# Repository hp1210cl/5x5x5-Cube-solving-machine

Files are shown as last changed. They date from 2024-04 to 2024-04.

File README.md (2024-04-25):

# 5x5x5 Cube solving machine

# 五阶解魔方机

一种自动复原5阶魔方的机器设计。A design of auto solving 5x5x5 cube machine.

*目前是已公开的最快的5阶解魔方机。The fastest 5x5x5 cube solving machine now.*

演示视频(demo video)：[三轴五阶解魔方机运行展示_哔哩哔哩_bilibili](https://www.bilibili.com/video/BV1yZ421n7nz/)

细节视频(detail video)：[3轴五阶解魔方机细节展示_哔哩哔哩_bilibili](https://www.bilibili.com/video/BV1LF4m1A7hH/)

### 1.整体架构

整个设计分为硬件和软件。

##### 1.1硬件部分

由框架、旋转器、推进器、arduino控制板和驱动板组成。

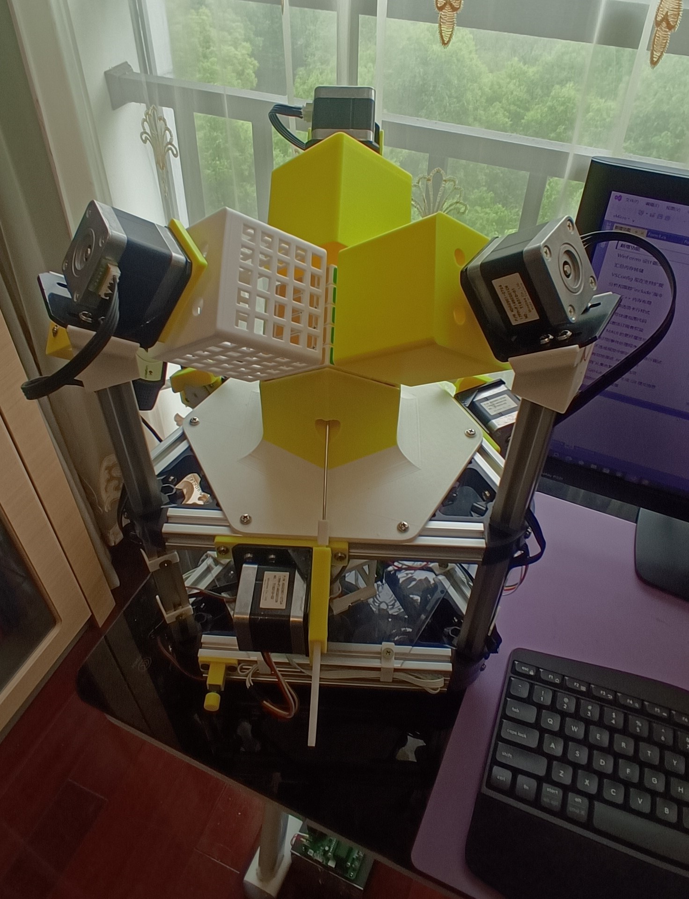
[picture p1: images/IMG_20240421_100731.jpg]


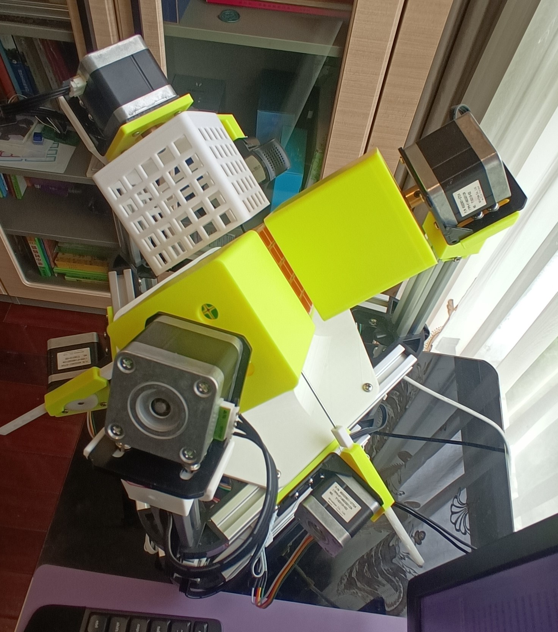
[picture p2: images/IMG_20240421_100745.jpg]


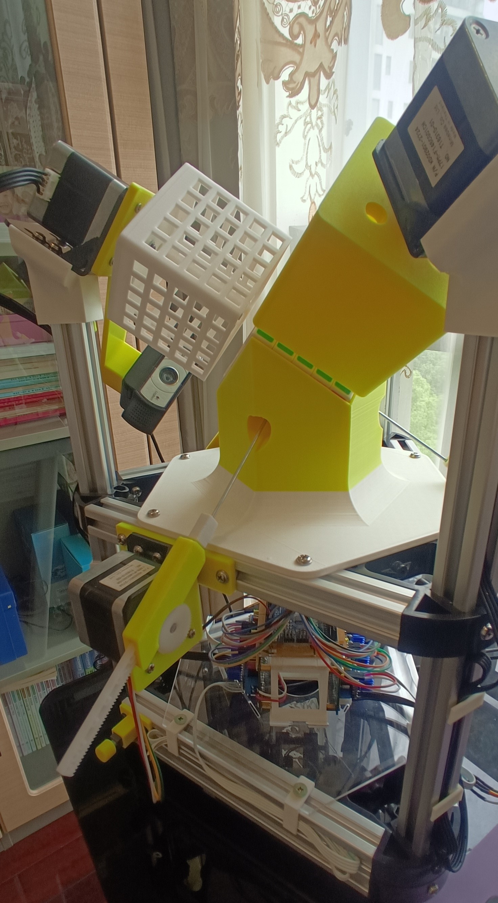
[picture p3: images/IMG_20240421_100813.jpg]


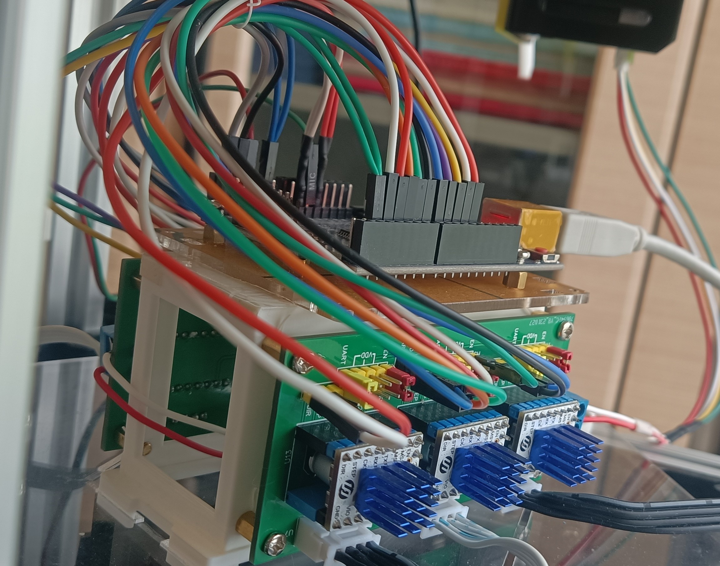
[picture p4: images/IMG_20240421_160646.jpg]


#### 1.2软件部分

由arduino下位机和PC上位机组成。

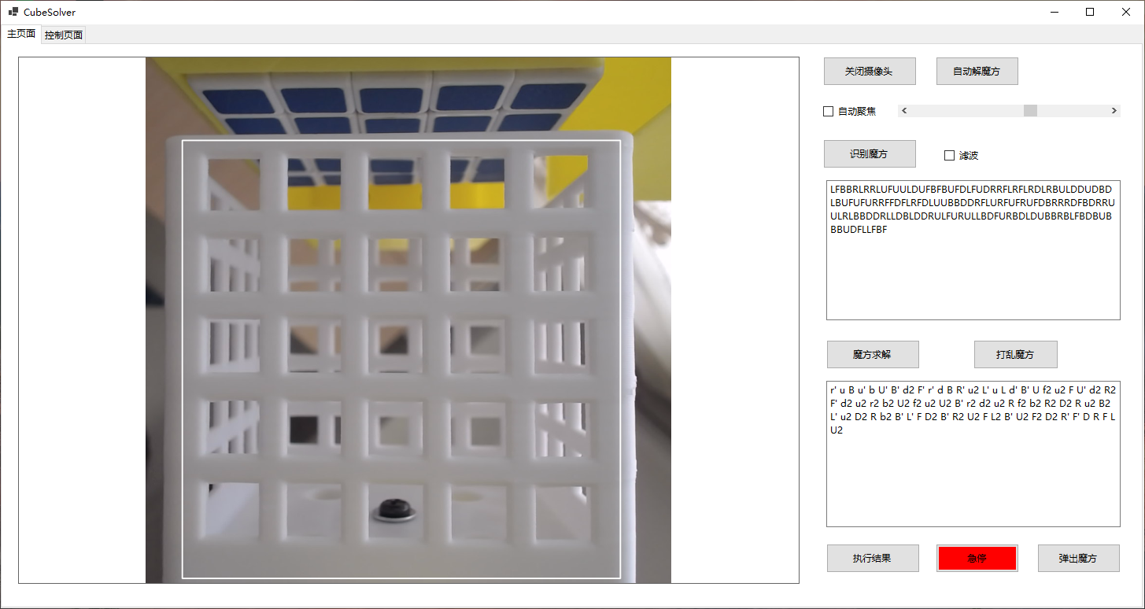
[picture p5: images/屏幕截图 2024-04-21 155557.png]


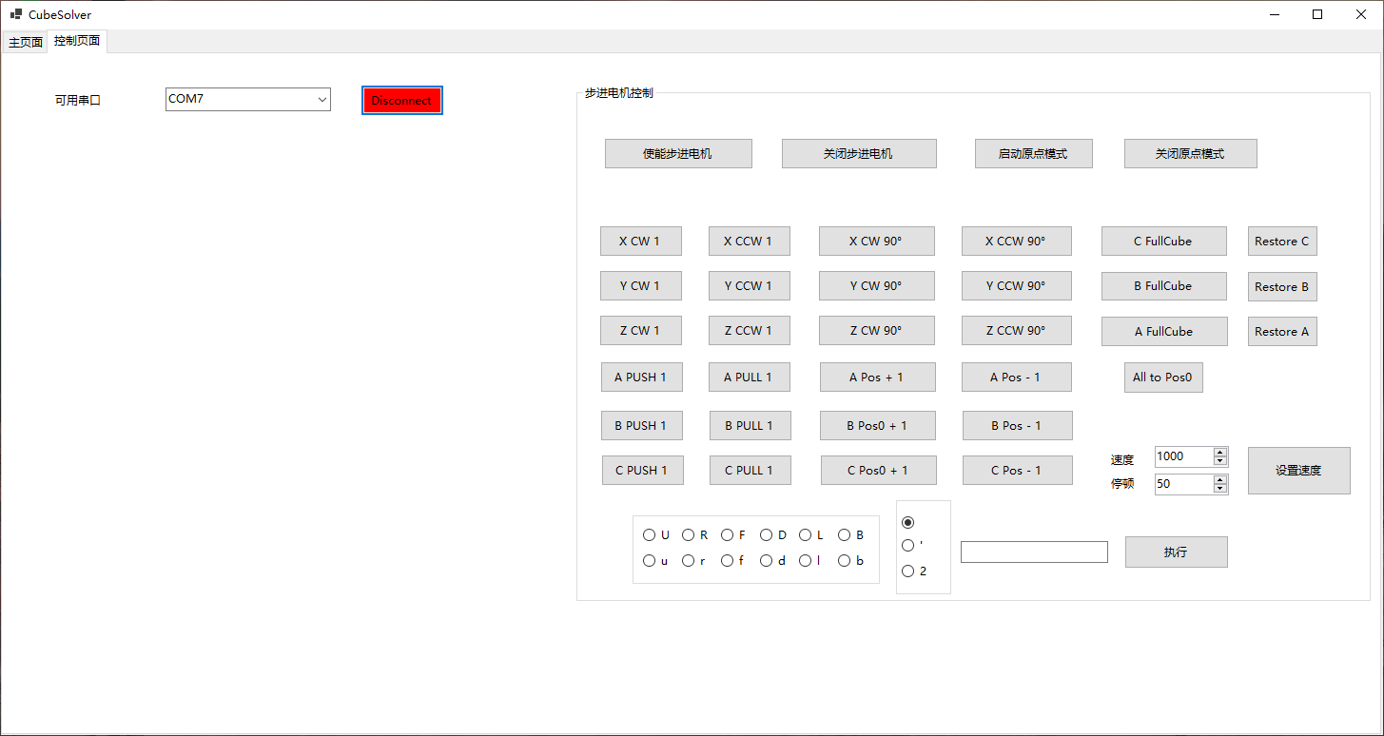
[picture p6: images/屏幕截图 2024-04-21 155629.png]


arduino下位机负责控制步进电机运动，PC上位机负责颜色识别、魔方求解、下位机控制等。

PC上位机使用VS2022 C#编写。

魔方求解使用了**陈霜**的五阶魔方算法，此算法是目前世界上最快的5阶算法，在此向他致敬！详情可以去他的github了解：[cs0x7f/cube555: 5x5x5 solver (github.com)](https://github.com/cs0x7f/cube555)，我也改写了c#版本：[hp1210cl/cube555-solver: C# version of Chen Shuang's Five-phase-reduction 5x5x5 solver (github.com)](https://github.com/hp1210cl/cube555-solver)。

颜色识别使用了EmguCV。

### 2.解魔方情况

对于一个打乱的5阶魔方，算法给出的步骤一般在70步左右。机器从识别-求解-复原全过程需耗时在90秒之内，典型时间75秒。

### 3.如何运行

#### 3.1硬件搭建

安装BOM清单准备好材料，按照图片成品组装。

#### 3.2下位机准备

将controller文件夹中的arduino程序刷入开发板。

#### 3.3运行上位机

将摄像头、arduino连接到PC，使用Visual Studio打开cubesolver文件夹下的工程文件，编译，运行。先打开摄像头，再在上位机控制选项卡页面连接开发板，再使能步进电机，进行机器的调试。

#### 3.4开始解魔方

如果出现卡滞，可以使用硬件紧急停止按钮，也可以使用上位机软件的急停按钮（有延时）。

### 4.调试细节

解魔方机需要精确调试才能顺利运行，具体调试详见调试文档。

###

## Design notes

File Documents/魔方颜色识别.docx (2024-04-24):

一、一些约定

1.X旋转器对着U，负责UD面的旋转，Y旋转器对着L，负责LR面的旋转，Z旋转器对着F，负责FB面的旋转。

2.A推杆负责UD层的控制，B推杆负责LR层的控制，C推杆负责FB层的控制。

3.魔方描述字符串采用标准的URFDLB定义。

4.以下顺时针逆时针是指面向旋转器看向步进电机，旋转器的转动方向。

二、识别控制流程

1.C推杆推送魔方到最高位，摄像头拍照得到Image1，Z旋转器顺时针整体转动魔方90度，摄像头拍照得到Image2，Z旋转器再次顺时针整体转动魔方90度，摄像头拍照得到Image3，Z旋转器再次顺时针整体转动魔方90度，摄像头拍照得到Image4，C推杆回位。

2.B推杆推送魔方到最高位，Y旋转器顺时针整体转动魔方90度，B推杆回位。

3.C推杆推送魔方到最高位，摄像头拍照得到Image5，Z旋转器顺时针整体转动魔方180度，摄像头拍照得到Image6.

三、识别方法

1.以上得到的6张照片，经过旋转（逆时针45度）、裁剪得到6张魔方单面的图片，就是魔方URFDLB表示法的视图。

2.当前魔方的U面是Image5（没有旋转变化），L面是Image1（旋转180度），F面是Image2（旋转180度），D面是Image6（旋转180度），R面是Image3（旋转180度），B面是Image4（旋转180度）。

3.每张图片有25个色块，判断每个色块的颜色，从左至右，从上至下，排列就得到面的描述字符串。

注：只针对摄像头特定安装位置（步进电机引出支架安装法）

四、颜色识别

1.将魔方单面的图片转换为HSV色域。

2.先按照黄色使用InRange将HSV图片二值化。

3.将二值化图片开操作去除白点。

4.将开操作的图片再闭操作去除黑点。

5.在闭操作的图片中查找轮廓。

6.对于每个色块的中心点，判断它是不是在这些轮廓中，如果在，那么这个色块就是黄色。

7.再按照红色、蓝色、橙色、绿色，重复1-6步。

8.剩下没有识别的色块就是白色。

9.对于U面，需要倒序，才是正确的面的描述字符串。

10.按照URFDLB的顺序，将面的描述字符串连接起来就是魔方的描述字符串。

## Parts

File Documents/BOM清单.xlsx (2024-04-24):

序号 | 名称 | 规格 | 数量 | 备注 | 示例图片
1 | 步进电机 | 42型 | 6 | 选用低内阻大扭矩高速型号，最好出轴长度12mm
2 | 六角联轴器 | 5mm | 3 | 铜 | #VALUE!
3 | 步进电机支架 | 42型 | 6 |  | #VALUE!
4 | 齿条 | 0.5m | 3 | 125*7*4mm | #VALUE!
5 | 齿轮 | 0.5m | 3 | 50齿，POM | #VALUE!
6 | Arduino模块 |  | 1 | UNO R3，其他开发板也可以 | #VALUE!
7 | TMC2209驱动模块 |  | 6 | 富源盛TMC2209 | #VALUE!
8 | 驱动底板 |  | 2 | 嘉立创免费制作 | #VALUE!
9 | 自锁开关 |  | 1 | 8x8.5x8.5 | #VALUE!
10 | 摄像头 | 罗技C930 | 1 | 其他型号也可以，1080P，有安装底座的最好
11 | 铝型材 | 20型 |  | 205mm的6根，350mm的3根
12 | 三角洲3D打印机角件 |  | 6 | 现在网上货比较少了，可以自行3D打印 | #VALUE!
13 | 螺丝、铝型材T型螺母 | 20型 | 若干 | M4*8 | #VALUE!
14 | 步进电机连接线 |  | 3 | 300mm
15 | 步进电机连接线 |  | 3 | 600mm
16 | 玩具车轴 |  | 3 | 2*80mm，铁 | #VALUE!
17 | 杜邦线 |  | 若干
18 | 24V电源模块 |  |  | 功率60W以上

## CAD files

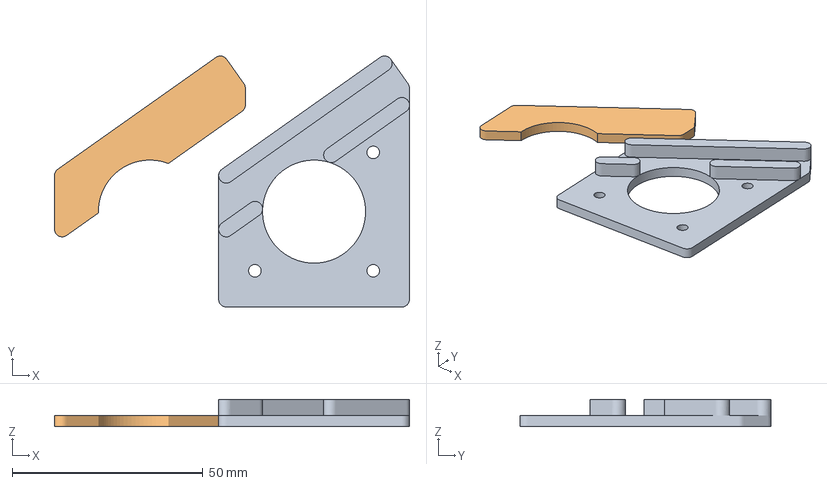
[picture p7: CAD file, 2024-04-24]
3D models/齿条推进支架50齿 v8.3mf
93.0 x 65.8 x 7.20 mm
实体4
实体5

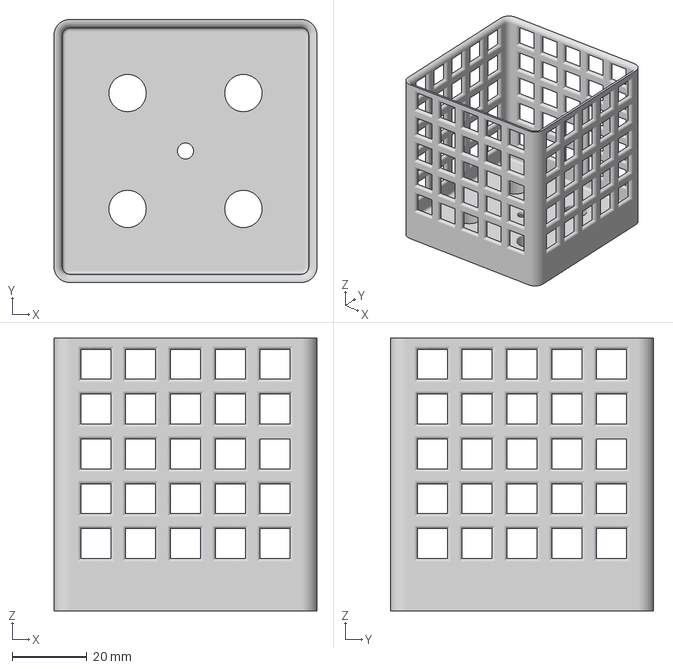
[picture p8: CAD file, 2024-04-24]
3D models/旋转器镂空 v2.3mf
70.4 x 70.4 x 73.0 mm

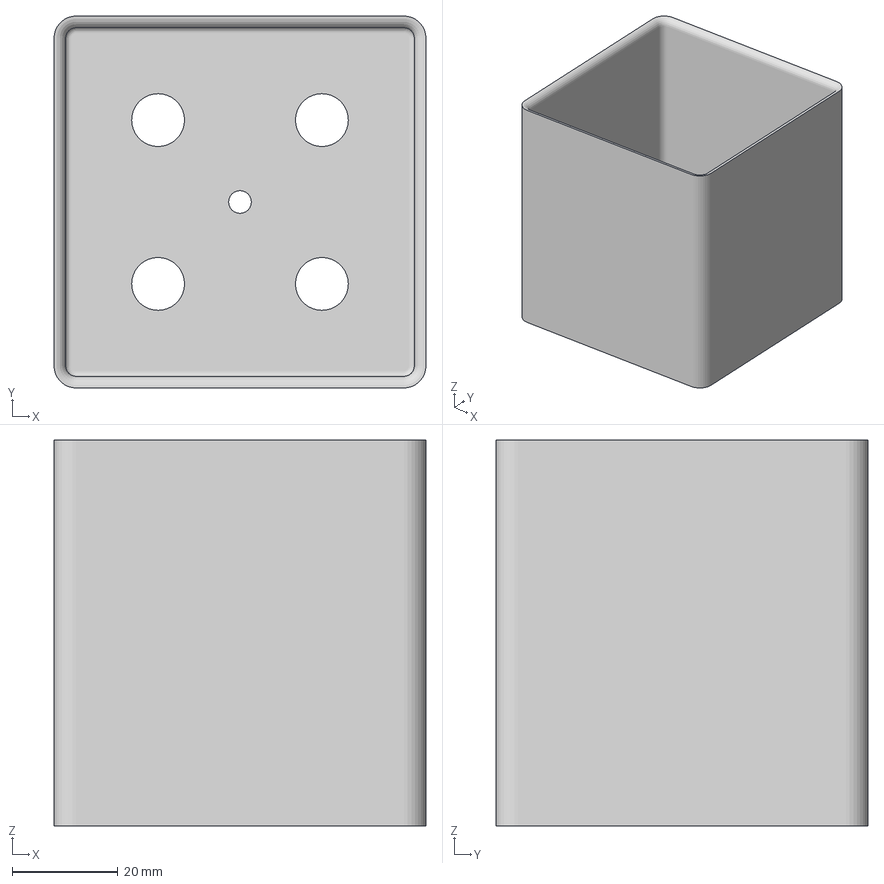
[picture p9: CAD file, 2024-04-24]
3D models/旋转器圆角 v4.3mf
70.4 x 70.4 x 73.0 mm

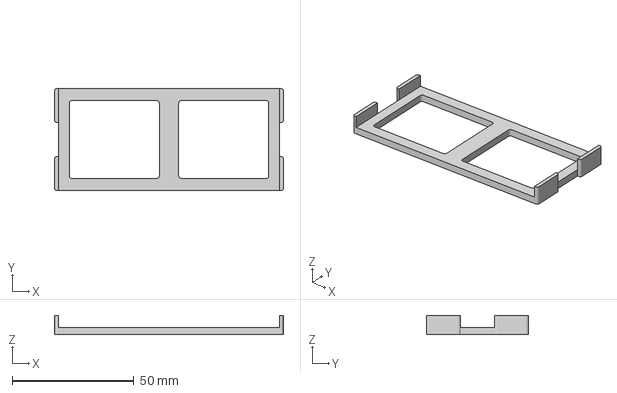
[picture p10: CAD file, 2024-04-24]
3D models/arduino安装架底板 v6.3mf
94.2 x 42.0 x 8.00 mm

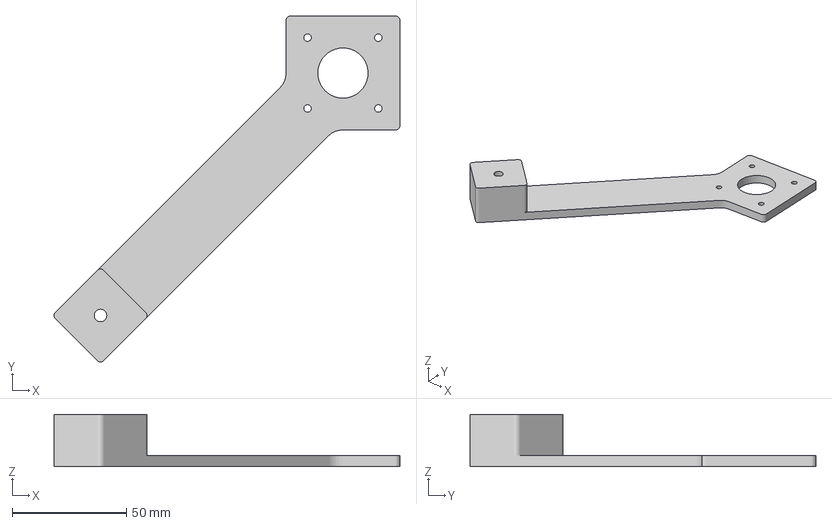
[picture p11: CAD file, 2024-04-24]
3D models/摄像头支架 v1.3mf
151.6 x 151.6 x 23.0 mm

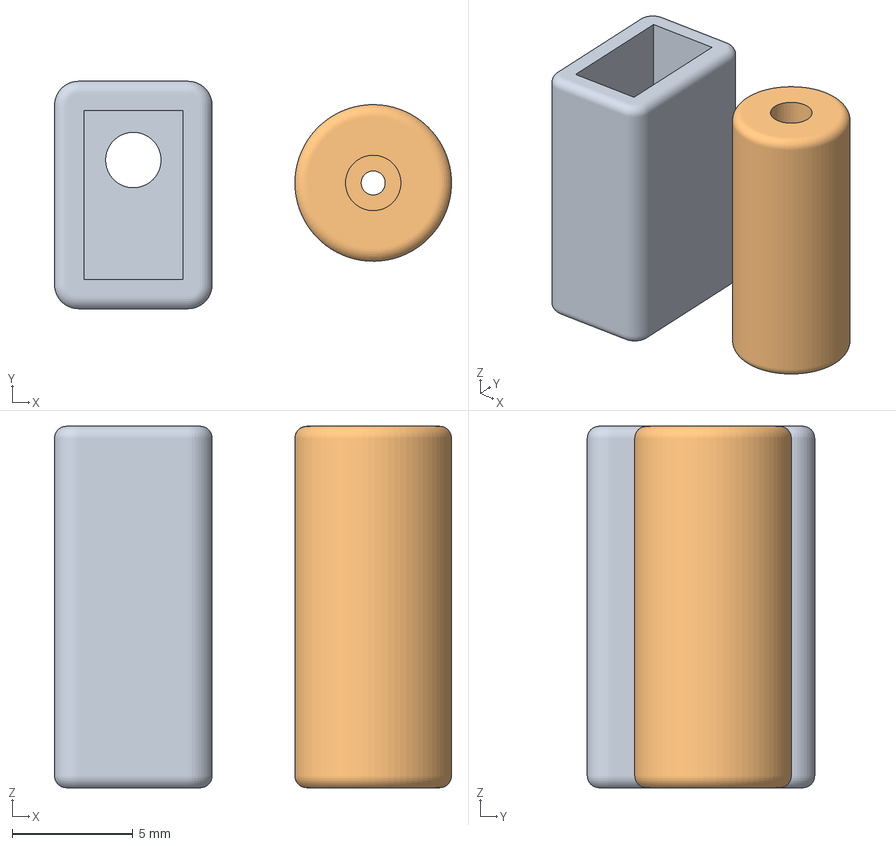
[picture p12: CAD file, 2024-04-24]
3D models/推杆端子 v1.3mf
16.5 x 9.44 x 15.0 mm
实体6
实体7

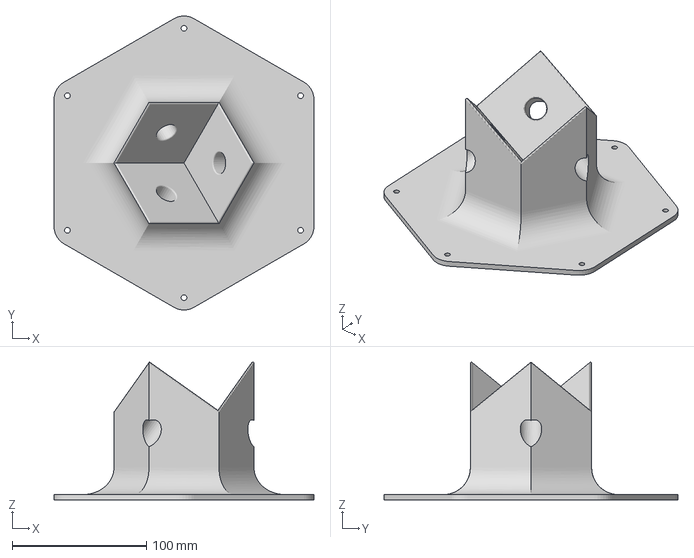
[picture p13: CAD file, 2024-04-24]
3D models/魔方底座 v13.3mf
194.0 x 219.3 x 102.8 mm

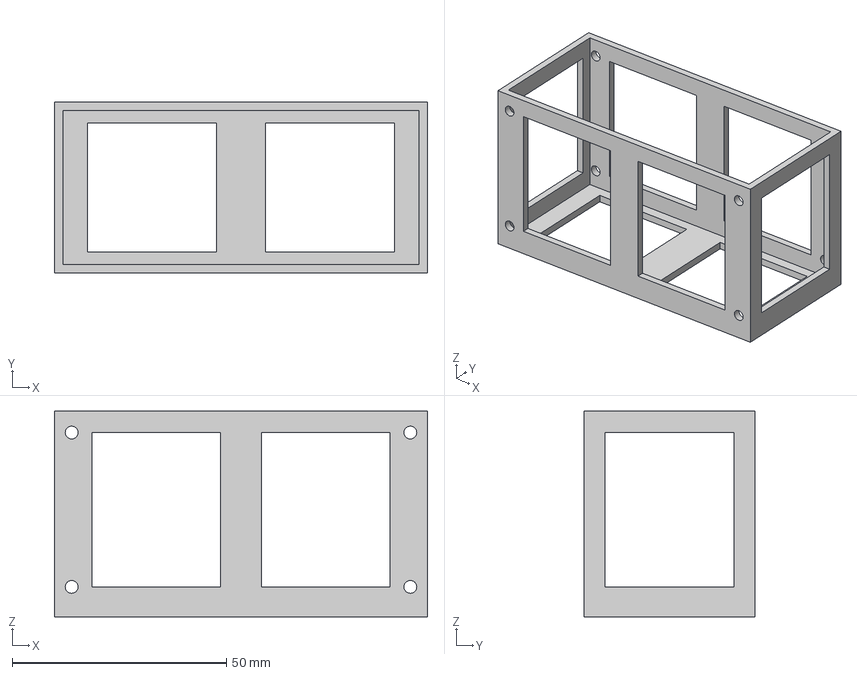
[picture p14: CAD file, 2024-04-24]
3D models/arduino安装架 v4.3mf
87.0 x 40.0 x 48.0 mm

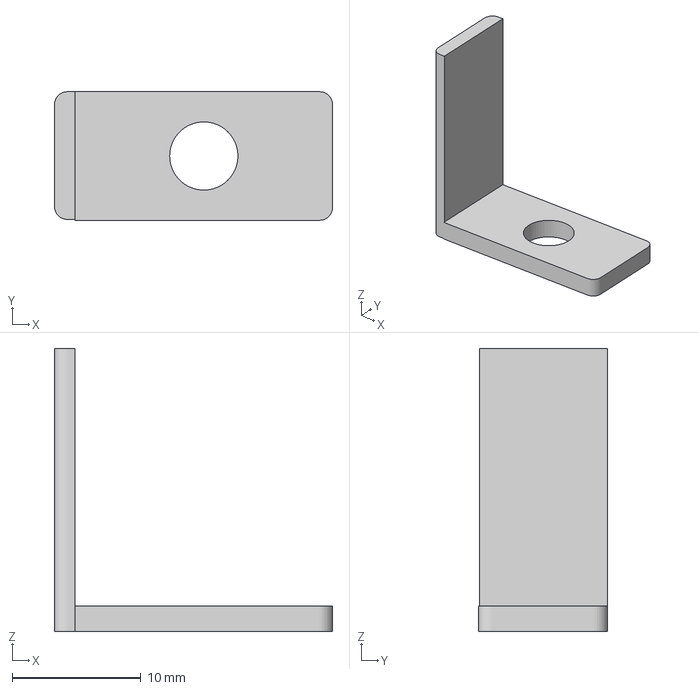
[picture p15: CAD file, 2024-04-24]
3D models/压线块 v1.3mf
21.6 x 10.0 x 22.0 mm

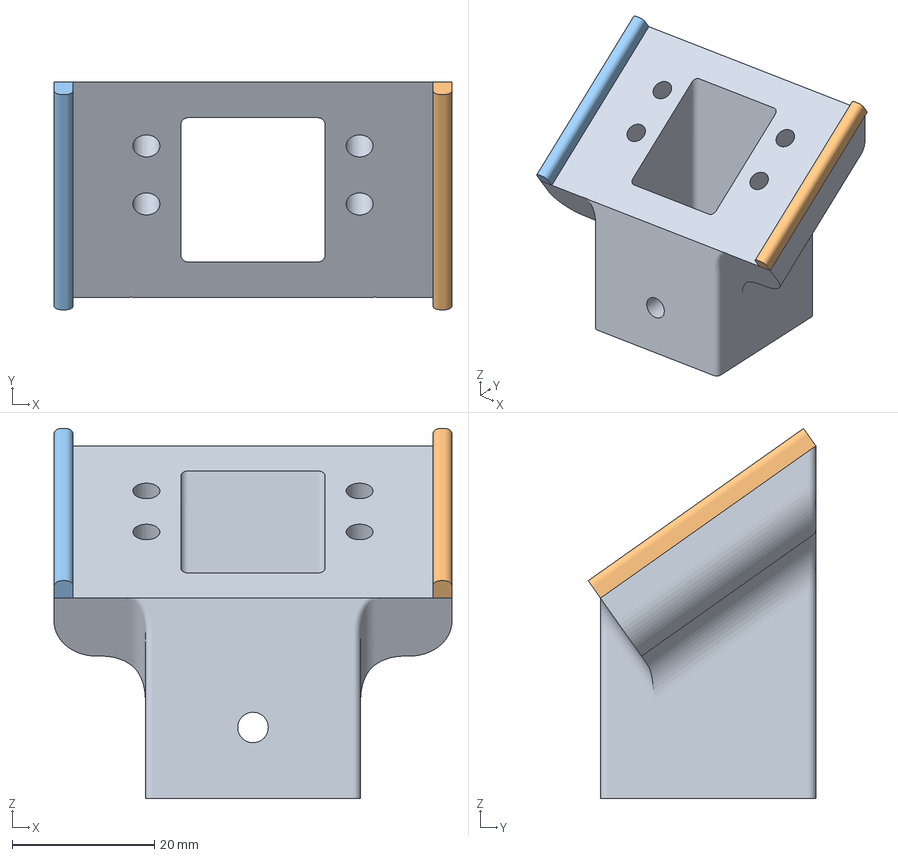
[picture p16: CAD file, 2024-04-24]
3D models/新步进电机支架 v3.3mf
56.0 x 32.0 x 52.1 mm
实体1
实体3
实体4

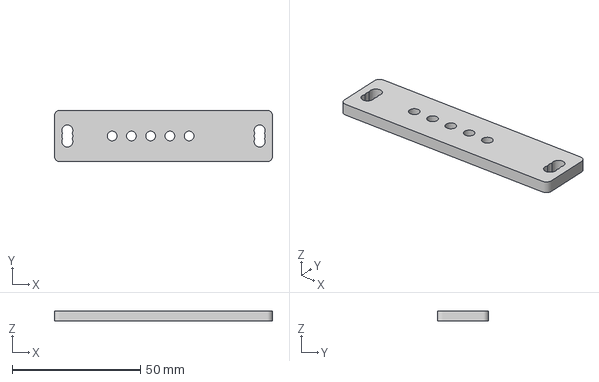
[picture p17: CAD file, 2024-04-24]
3D models/推进器安装板 v3.3mf
85.0 x 20.0 x 4.00 mm

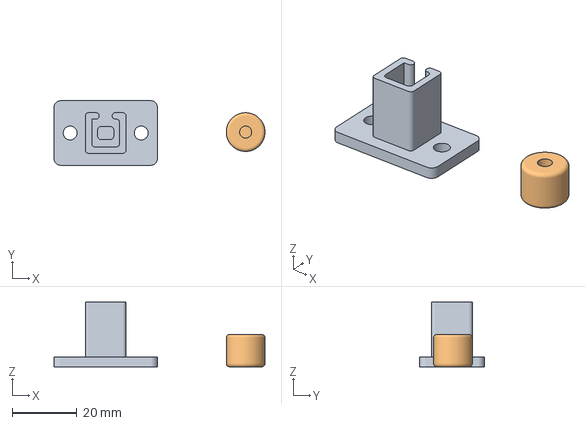
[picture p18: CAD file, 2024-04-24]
3D models/紧急停止按钮 v7.3mf
65.3 x 20.0 x 20.0 mm
实体3
实体5

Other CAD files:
3D models/紧急停止按钮 v6.3mf

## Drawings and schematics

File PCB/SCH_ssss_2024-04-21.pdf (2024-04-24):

### VDD

### VCC

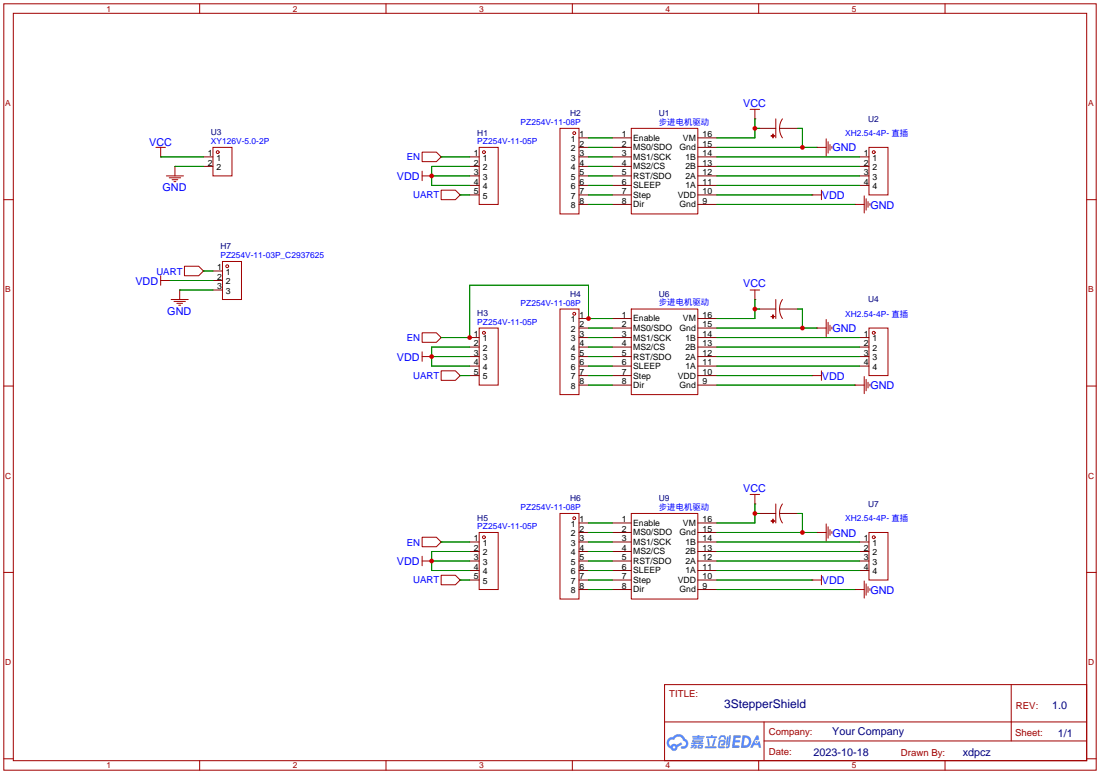
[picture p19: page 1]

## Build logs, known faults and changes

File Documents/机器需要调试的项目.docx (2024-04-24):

机器需要调试的项目

（解魔方机需要精确调试才能顺利运行）

1.步进电机驱动电流

根据步进电机的选型，确定步进电机的额定电流。Arduino控制器使用UART通讯设置TMC2209，使能了模拟电流调整，运行电流设为100%。所以需要调整TMC2209模块的电位计，使其RMS电流与步进电机的额定电流一致，否则会导致电机过热或者电机丢步。

2.初始位置调整

2.1旋转器初始位置

要保证旋转器的边与魔方底座的边平行，并且距离相等（一般距离以魔方单层高度为限）。无论是正俯视还是以任意魔方底座侧面棱线为中心看，机器都应是对称结构。如果不对称，使用上位机微调步进电机或者调整魔方底座的安装位置或者检查旋转器的安装对称性。

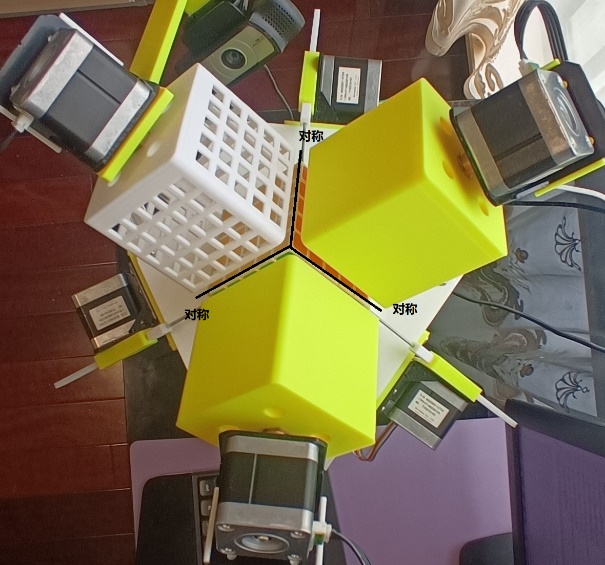
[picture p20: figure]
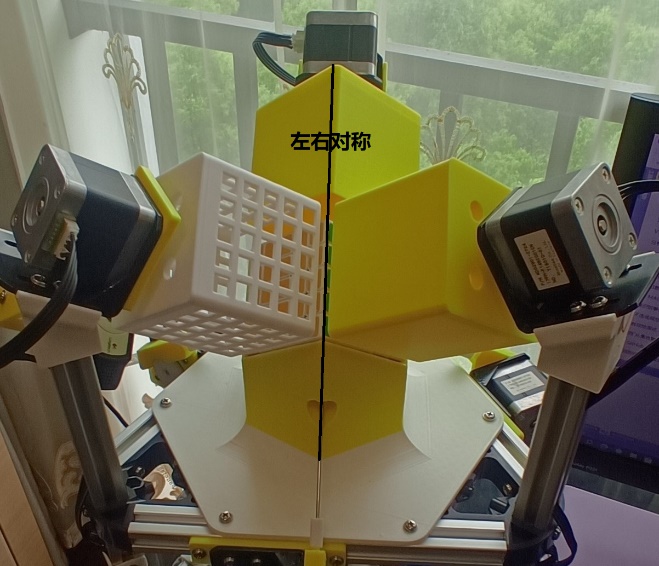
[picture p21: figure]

2.2齿条推进装置的初始位置

先试用上位机单步推动魔方，再回撤，直至魔方不再有运动后，继续回撤4步，即为齿条推进装置的初始位置。

3.摄像头的调整

要确保上位机中摄像头捕获的画面中魔方的面在白色框中。

4.魔方颜色识别的调整

由于魔方品牌较多，颜色各有差别，如果颜色识别不准确，需要调整源代码中常量代码中HSV颜色分量最大值和最小值。颜色识别过程可以查看可执行文件目录下生成的调试暂存图片，每个魔方面每种颜色（无白色）一张暂存图片。

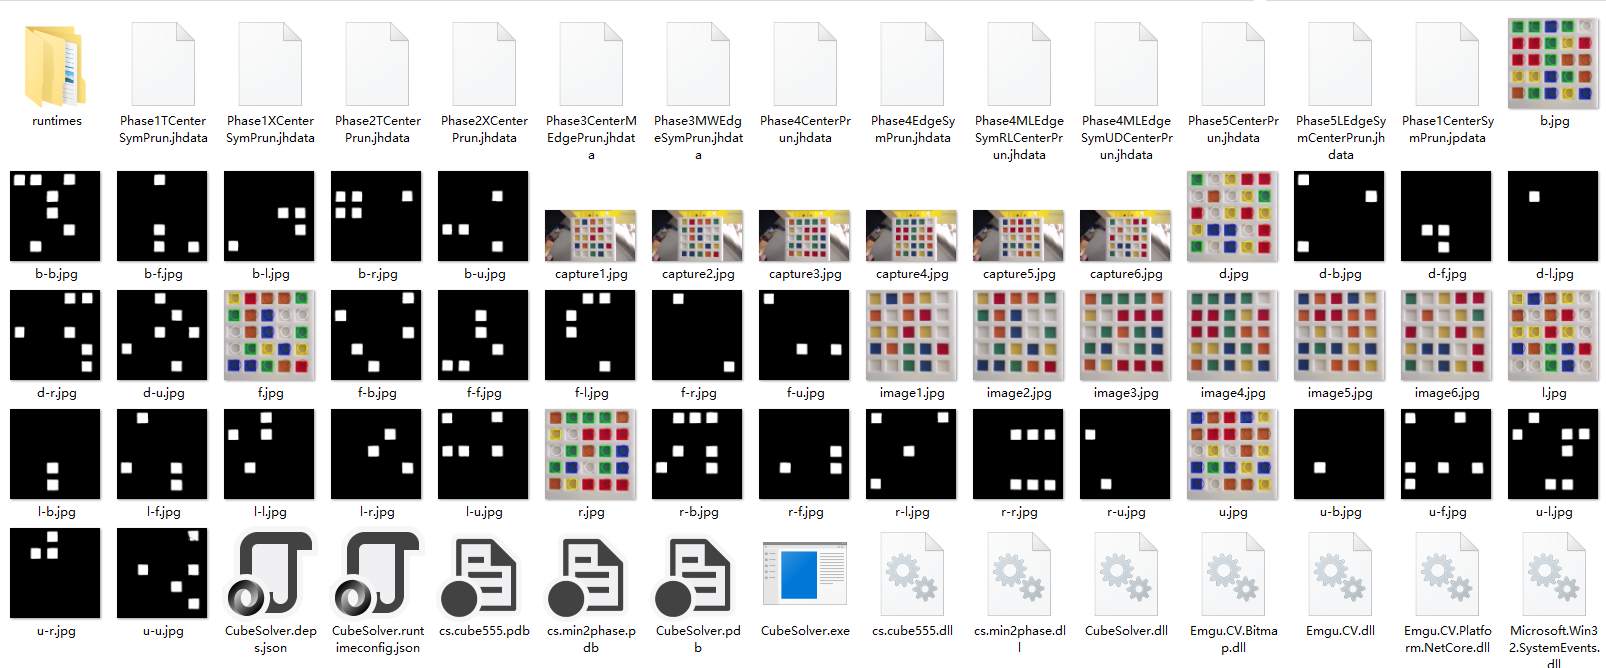
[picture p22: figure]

5.运行一段时间调整

各紧固件的紧固程度，特别是旋转器与联轴器的连接。

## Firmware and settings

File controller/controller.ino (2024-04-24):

#include <TMC2209.h>
#include <SoftwareSerial.h>

//
//TMC2209 direction is opposite to A4988
//
#define PAUSE    A3
#define EN       2
#define X_STEP   4
#define X_DIR    3
#define Y_STEP   8
#define Y_DIR    7
#define Z_STEP   12
#define Z_DIR    11
#define A_STEP   A5
#define A_DIR    A4
#define B_STEP   10
#define B_DIR    9
#define C_STEP   6
#define C_DIR    5
#define SPEED    750
#define PAUSE_TIME 30
#define RX_PIN   A0
#define TX_PIN   A1
#define RUN_CURRENT_PERCENT   100
#define HOLD_CURRENT_PERCENT   70
#define HOLD_DELAY_CURRENT_PERCENT   50
#define MAX_ABC_STEP_COUNT   500
SoftwareSerial soft_serial(RX_PIN, TX_PIN);

byte cmdData[6];
int cmdByte = 0;
int count = 0;
char header;
int steps0;
int steps1;
bool originalMode = false;
int aStepCount;
int bStepCount;
int cStepCount;
int speed = SPEED;
int pausetime = PAUSE_TIME;

// Instantiate TMC2209
TMC2209 stepper_driver;

void doSteps(int pin, int steps) {
    for (int i = 0; i < steps; i++) {
        if (digitalRead(PAUSE)==LOW) return;
        digitalWrite(pin, HIGH);
        delayMicroseconds(speed);
        digitalWrite(pin, LOW);
        delayMicroseconds(speed);
    }
}

void setup() {

    pinMode(PAUSE, INPUT_PULLUP);
    pinMode(EN, OUTPUT);
    digitalWrite(EN, HIGH);
    pinMode(X_DIR, OUTPUT);
    pinMode(X_STEP, OUTPUT);
    pinMode(Y_DIR, OUTPUT);
    pinMode(Y_STEP, OUTPUT);
    pinMode(Z_DIR, OUTPUT);
    pinMode(Z_STEP, OUTPUT);
    pinMode(A_DIR, OUTPUT);
    pinMode(A_STEP, OUTPUT);
    pinMode(B_DIR, OUTPUT);
    pinMode(B_STEP, OUTPUT);
    pinMode(C_DIR, OUTPUT);
    pinMode(C_STEP, OUTPUT);


    // initialize serial:
    Serial.begin(115200);

    stepper_driver.setup(soft_serial);
}

void initTMC2209() {

    stepper_driver.setHardwareEnablePin(EN);
    //stepper_driver.enableCoolStep();
    //stepper_driver.setAllCurrentValues(RUN_CURRENT_PERCENT, HOLD_CURRENT_PERCENT, HOLD_DELAY_CURRENT_PERCENT);
    stepper_driver.setMicrostepsPerStep(2);
    //stepper_driver.enableStealthChop();
    stepper_driver.setStandstillMode(TMC2209::BRAKING);
    stepper_driver.useExternalSenseResistors();
    stepper_driver.enableAnalogCurrentScaling();//Vref=2.13V,Irms=0.707*2.13=1.5A
    stepper_driver.disableAutomaticCurrentScaling();
    //  stepper_driver.moveUsingStepDirInterface();
    stepper_driver.setPwmOffset(64);
    stepper_driver.setPwmGradient(64);
    stepper_driver.setRunCurrent(RUN_CURRENT_PERCENT);
    stepper_driver.setHoldCurrent(HOLD_CURRENT_PERCENT);
    stepper_driver.disable();

}

void loop() {


    if (Serial.available())
    {
        // get the new byte:
        cmdByte = Serial.read();
        count = count + 1;
        cmdData[count - 1] = cmdByte;
        if (cmdByte == '\n') // \0x0A
        {
            if (count == 6)
            {
                header = cmdData[0];
                steps0 = cmdData[1] << 8 | cmdData[2];
                steps1 = cmdData[3] << 8 | cmdData[4];
                //Serial.print(header);
                //Serial.print(" ");
                //Serial.print(steps0);
                //Serial.print(" ");
                //Serial.println(steps1);
                switch (header)
                {
                case 'E':
                    if (steps0 == 0) {
                        stepper_driver.disable();
                    }
                    else {
                        initTMC2209();
                        stepper_driver.enable();
                    }
                    break;
                case 'O':
                    if (steps0 == 0) {
                        originalMode = false;
                    }
                    else {
                        aStepCount = 0;
                        bStepCount = 0;
                        cStepCount = 0;
                        originalMode = true;
                    }
                    break;
                case 'S':
                    if (steps0 > 0) {
                        speed = steps0;
                    }
                    if (steps1 > 0) {
                        pausetime = steps1;
                    }
                    break;
                case 'X':
                    if (steps0 > 0) {
                        digitalWrite(X_DIR, LOW);
                        doSteps(X_STEP, steps0);
                    }
                    else if (steps0 < 0) {
                        digitalWrite(X_DIR, HIGH);
                        doSteps(X_STEP, -steps0);
                    }
                    delay(pausetime);
                    if (steps1 > 0) {
                        digitalWrite(X_DIR, LOW);
                        doSteps(X_STEP, steps1);
                    }
                    else if (steps1 < 0) {
                        digitalWrite(X_DIR, HIGH);
                        doSteps(X_STEP, -steps1);
                    }            
                    delay(pausetime);
                    break;
                case 'Y':
                    if (steps0 > 0) {
                        digitalWrite(Y_DIR, LOW);
                        doSteps(Y_STEP, steps0);
                    }
                    else if (steps0 < 0) {
                        digitalWrite(Y_DIR, HIGH);
                        doSteps(Y_STEP, -steps0);
                    }
                    delay(pausetime);
                    if (steps1 > 0) {
                        digitalWrite(Y_DIR, LOW);
                        doSteps(Y_STEP, steps1);
                    }
                    else if (steps1 < 0) {
                        digitalWrite(Y_DIR, HIGH);
                        doSteps(Y_STEP, -steps1);
                    }
                    delay(pausetime);
                    break;
                case 'Z':
                    if (steps0 > 0) {
                        digitalWrite(Z_DIR, LOW);
                        doSteps(Z_STEP, steps0);
                    }
                    else if (steps0 < 0) {
                        digitalWrite(Z_DIR, HIGH);
                        doSteps(Z_STEP, -steps0);
                    }
                    delay(pausetime);
                    if (steps1 > 0) {
                        digitalWrite(Z_DIR, LOW);
                        doSteps(Z_STEP, steps1);
                    }
                    else if (steps1 < 0) {
                        digitalWrite(Z_DIR, HIGH);
                        doSteps(Z_STEP, -steps1);
                    }
                    delay(pausetime);
                    break;
                case 'A':
                    if (originalMode) 
                    {
                        if (aStepCount + steps0 < 0) {
                            break;
                        }
                        else if (aStepCount + steps0 > MAX_ABC_STEP_COUNT)
                        {
                            break;
                        }
                        else
                        {
                            aStepCount += steps0;
                        }
                    }
                    if (steps0 > 0) {
                        digitalWrite(A_DIR, LOW);
                        doSteps(A_STEP, steps0);
                    }
                    else if (steps0 < 0) {
                        digitalWrite(A_DIR, HIGH);
                        doSteps(A_STEP, -steps0);
                    }
                    delay(pausetime);
                    break;
                case 'B':
                    if (originalMode)
                    {
                        if (bStepCount + steps0 < 0) {
                            break;
                        }
                        else if (bStepCount + steps0 > MAX_ABC_STEP_COUNT)
                        {
                            break;
                        }
                        else
                        {
                            bStepCount += steps0;
                        }
                    }
                    if (steps0 > 0) {
                        digitalWrite(B_DIR, LOW);
                        doSteps(B_STEP, steps0);
                    }
                    else if (steps0 < 0) {
                        digitalWrite(B_DIR, HIGH);
                        doSteps(B_STEP, -steps0);
                    }
                    delay(pausetime);
                    break;
                case 'C':
                    if (originalMode) 
                    {
                        if (cStepCount + steps0 < 0) {
                            break;
                        }
                        else if (cStepCount + steps0 > MAX_ABC_STEP_COUNT)
                        {
                            break;
                        }
                        else
                        {
                            cStepCount += steps0;
                        }
                    }
                    if (steps0 > 0) {
                        digitalWrite(C_DIR, LOW);
                        doSteps(C_STEP, steps0);
                    }
                    else if (steps0 < 0) {
                        digitalWrite(C_DIR, HIGH);
                        doSteps(C_STEP, -steps0);
                    }
                    delay(pausetime);
                    break;
                default:
                    break;
                }
                Serial.println("EOD");//End Of Do
            }
            count = 0;
            cmdData[0] = 0;
            cmdData[1] = 0;
            cmdData[2] = 0;
            cmdData[3] = 0;
            cmdData[4] = 0;
            cmdData[5] = 0;
        }
    }

}
